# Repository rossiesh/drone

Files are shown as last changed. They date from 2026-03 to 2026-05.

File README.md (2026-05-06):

# ESP32-S3 Drone

## Status

Work in progress.

## Overview

This repository contains the firmware, 3D-print resources and documentation for a drone project based on two XIAO ESP32-S3 boards:

- one ESP32-S3 as the flight controller
- one ESP32-S3 used in the handheld

The long-term goal is a custom drone system with:

- ESP-NOW communication between handheld and flight controller
- a custom flight control stack
- an Android app connected to the handheld via USB-C for displaying telemetry data 
- 3D-printed drone parts

## Current state

The current implementation already covers some core building blocks:

- ESP-NOW communication between handheld and flight controller is set up
- the MPU6500 IMU is connected via SPI and can be read successfully
- gyroscope calibration is implemented
- 3D print resources

The project is still missing major parts required for actual flight, for example:

- control packet/telemetry packet integration
- full flight-control logic
- motor mixer logic
- Android app
- full preflight/safety/failsafe handling

## Repository structure

- [`esp32_fc/`](./esp32_fc/) ESP-IDF project for the flight controller

- [`esp32_handheld/`](./esp32_handheld/) ESP-IDF project for the handheld

- [`protocols/`](./protocols/) shared packet structures for control/telemetry communication

- [`android_app/`](./android_app/) Android application code

- [`print_resources/`](./print_resources/) 3D print files and further information

- [`documentation/`](./documentation/) project documentation such as materials and assembly information

- [`tools/`](./tools/) helper tools

## Development environment

- VS Code
- ESP-IDF extension 
- ESP-IDF v6.0
- target: esp32s3

## Documentation

- [Materials](documentation/materials.md)
- [Assembly tutorial](documentation/assembly_tutorial.md)
- [Print resources](print_resources/README.md)

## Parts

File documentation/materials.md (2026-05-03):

## Materials

- FC and controller: 2x XIAO ESP32 S3 *(~15€ for the three-pack)*
- IMU: MPU6500 *(~3€)*
- barometer: MS5611 *(~5€)*
- ESC: Sequre Blueson A2 (comes with power cables, XT60 connector and capacitor) *(~30€)*
- motors: 4x iFlight XING-E Pro 2207 2450KV (screws and self-locking nuts included) *(~35€)* or similar
- props: 4x iFlight Nazgul F5 *(~5€)*
- battery: e.g. Goldbat 4s 1500mAh LiPo *(~35€ for a two-pack)* (an additional LiPo charger is required)
- generic DC-DC 3A adjustable buck converter, e.g. MP1584EN *(~4€ for the five-pack)*
- 2.4GHz rod antenna (2.81dBi) for Seeed Studio XIAO *(~3€)*
- M3 screw set with nuts and screwdriver/ratchet wrench *(~8€ for the screw set)*, you need:
  - 24x M3x12 (16 with flats)
  - 12x M3x16 with flats
  - 6x M3x30
  - 12x locks
- M3 silicon shock absorber rings *(~3€)*, you need 18 rings
- 3D printer for the frame (Elegoo Neptune 4) *(~200€)* 
- White & black Elegoo Pla+ *(~20€ per spool)*
- soldering equipment: 
  - basic soldering iron *(~20€)*
  - 900M-T-I soldering tips recommend when working with the ESP32 & sensors *(~5€)*
  - brass wool for cleaning *(~5-10€)*
  - tip re-tiner *(~5€)*
- basic multimeter *(~15-20€)*
- high AWG cables, e.g. breadboard jumper wires
- crimping pliers with JST-XH 2.5mm connectors *(~25€ for a full set)*
- double sided tape

Most of the items I got from AliExpress.

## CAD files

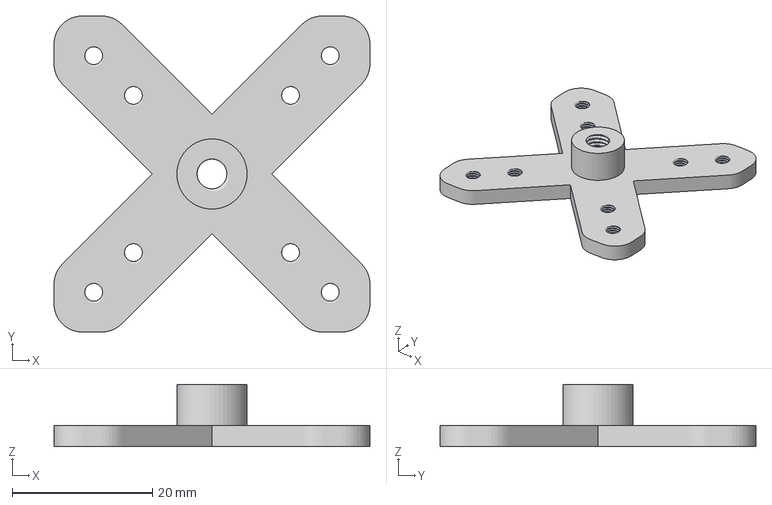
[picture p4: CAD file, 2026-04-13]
print_resources/bottom_plate.3mf
45.0 x 45.0 x 8.90 mm

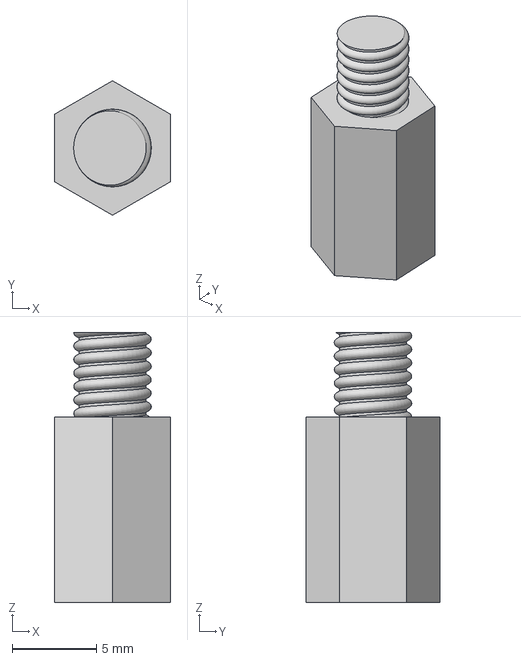
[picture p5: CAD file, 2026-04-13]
print_resources/landing_gear_long.3mf
6.90 x 7.97 x 16.0 mm

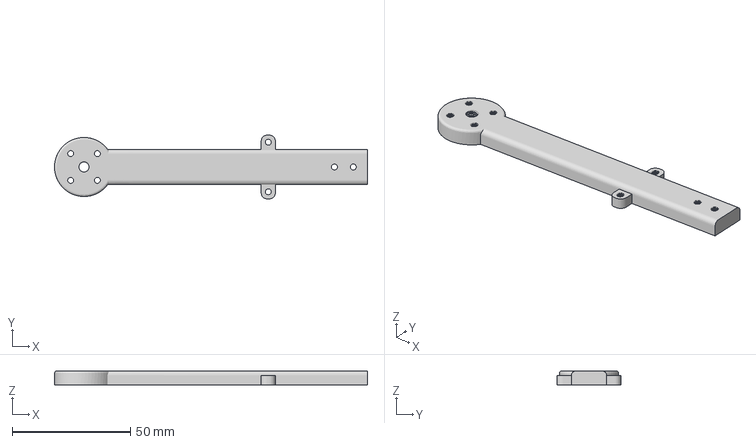
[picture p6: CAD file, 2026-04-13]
print_resources/arm.3mf
132.5 x 27.0 x 6.00 mm

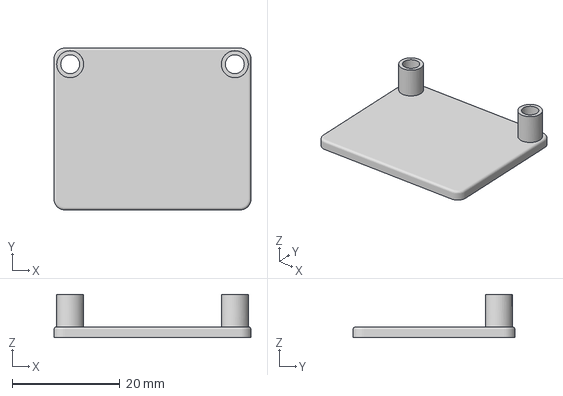
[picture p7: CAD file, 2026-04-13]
print_resources/e_plate_bottom.3mf
36.5 x 30.0 x 8.00 mm

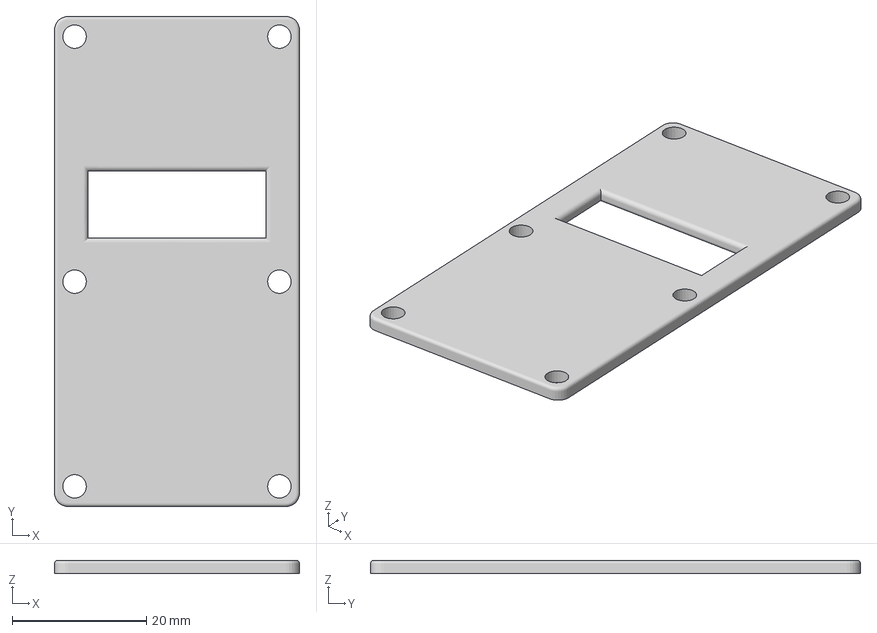
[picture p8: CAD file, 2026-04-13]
print_resources/e_plate_top.3mf
36.5 x 73.0 x 2.00 mm

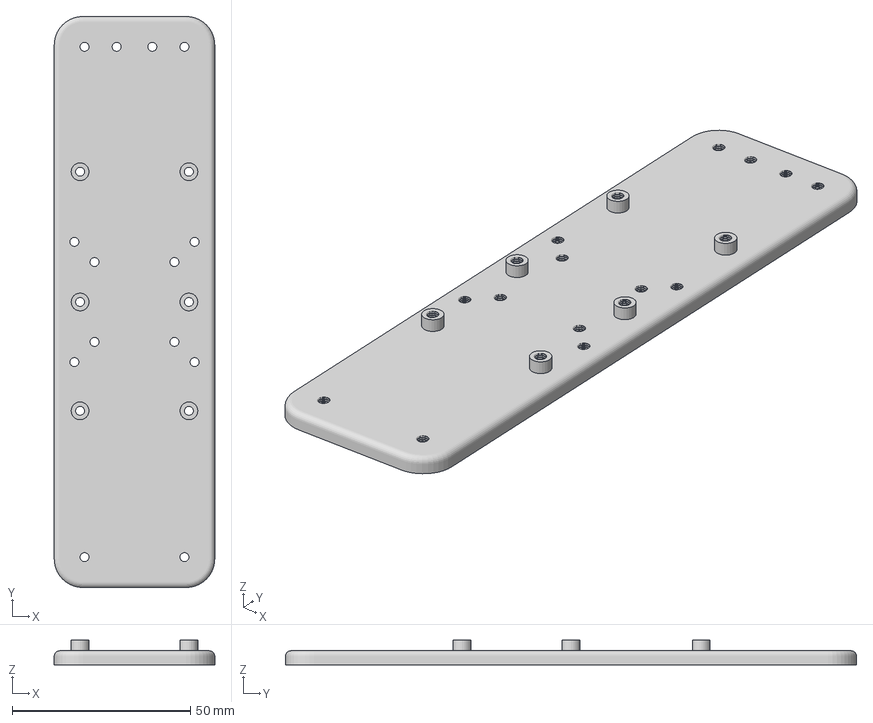
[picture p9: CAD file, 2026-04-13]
print_resources/middle_plate.3mf
45.0 x 160.0 x 7.00 mm

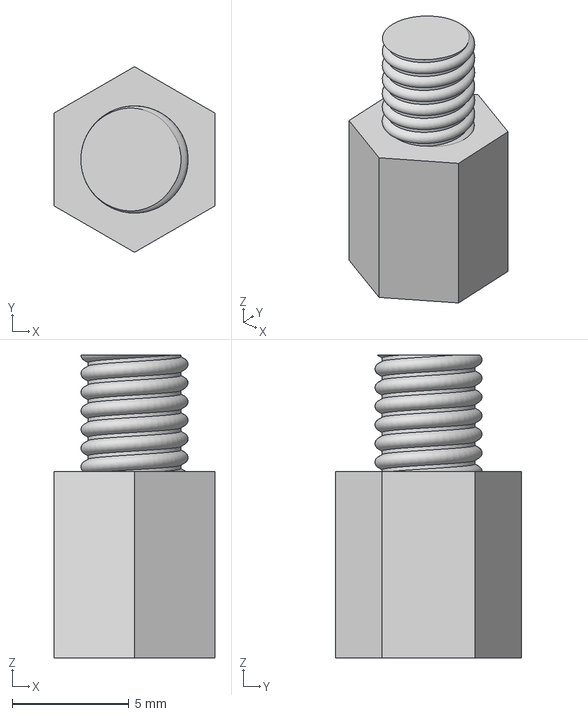
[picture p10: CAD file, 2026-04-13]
print_resources/landing_gear_short.3mf
6.90 x 7.97 x 13.0 mm

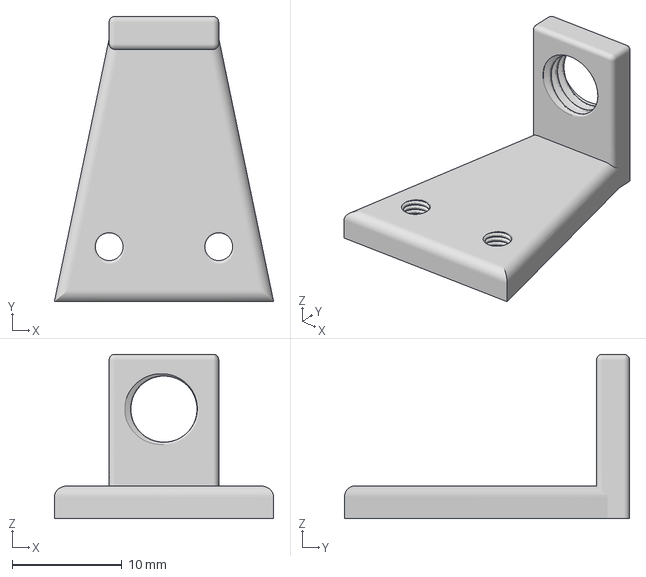
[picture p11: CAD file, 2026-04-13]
print_resources/antenna_holder.3mf
20.0 x 26.0 x 15.0 mm

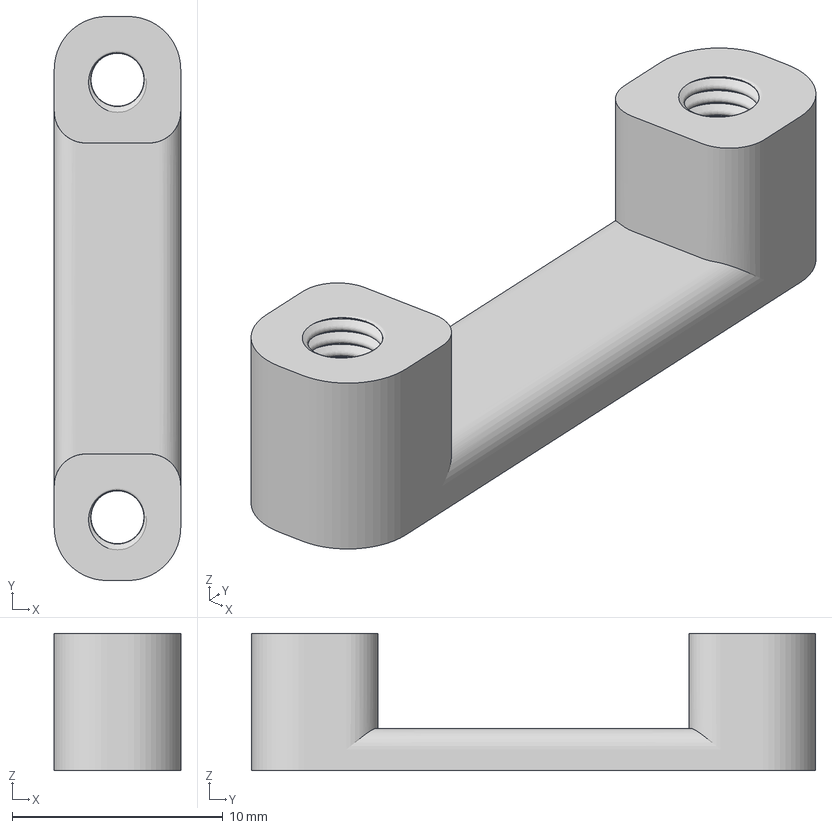
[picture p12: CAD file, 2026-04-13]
print_resources/cable_holder.3mf
6.00 x 26.8 x 6.50 mm

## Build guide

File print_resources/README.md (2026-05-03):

## General information

- printer used: Elegoo Neptune 4
- filament: Elegoo Pla+
- black Pla+ for the landing gear and plates for the electronics
- white Pla+ for the body parts and arms due to better heat reflection than black Pla+
- print arm.3mf four times
- print cable_holder.3mf four times
- print landing_gear_long.3mf four times
- print everything else one time
- use drone_arms.curaprofile only for the arms
- use drone_electronics_plates.curaprofile for:
  - e_plate_bottom.3mf
  - e_plate_top.3mf
- use drone_main_body.curaprofile for:
  - antenna_holder.3mf
  - bottom_plate.3mf
  - cable_holder.3mf
  - landing_gear_long.3mf
  - landing_gear_short.3mf
  - middle_plate.3mf

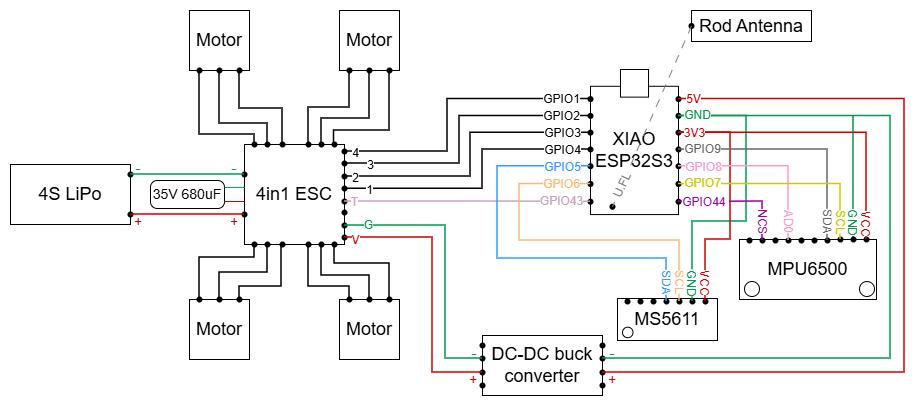
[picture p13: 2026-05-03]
documentation/assets/diagrams/wiring_diagram_drone.png

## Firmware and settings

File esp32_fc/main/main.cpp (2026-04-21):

#include <stdio.h>
#include "wifi.h"
#include "espnow.h"
#include "esp_log.h"
#include "mpu6500.h"
#include "freertos/FreeRTOS.h"
#include "freertos/task.h"

static const char *TAG = "mpu6500";

extern "C" void app_main(void)
{
    ESP_ERROR_CHECK(wifi_init());
    ESP_ERROR_CHECK(espnow_init());
    ESP_ERROR_CHECK(mpu6500_init());
    ESP_ERROR_CHECK(mpu6500_calibrate_gyro());
    ImuData imu_data = {0};
    while (true)
    {
        ESP_ERROR_CHECK(mpu6500_read_data(imu_data));
        ESP_LOGI(TAG, "a_x:%6d a_y=%6d a_z=%6d temp=%6d g_x=%6d g_y=%6d g_z=%6d", imu_data.a_x, imu_data.a_y, imu_data.a_z, imu_data.temp, imu_data.g_x, imu_data.g_y, imu_data.g_z);
        vTaskDelay(pdMS_TO_TICKS(100));
    }
}

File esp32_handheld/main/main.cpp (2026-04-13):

#include <stdio.h>
#include "control_packet.h"
#include "wifi.h"
#include "espnow.h"
#include "driver/gpio.h"
#include "freertos/FreeRTOS.h"
#include "freertos/task.h"
#include "esp_log.h"

void setup_gpio_pin(gpio_num_t gpio_num)
{
    gpio_config_t io_conf = {
        .pin_bit_mask = 1ULL << gpio_num,
        .mode = GPIO_MODE_INPUT,
        .pull_up_en = GPIO_PULLUP_ENABLE,
        .pull_down_en = GPIO_PULLDOWN_DISABLE,
        .intr_type = GPIO_INTR_DISABLE,
    };
    ESP_ERROR_CHECK(gpio_config(&io_conf));
}

extern "C" void app_main(void)
{
    static const char *TAG = "button_num";

    ESP_ERROR_CHECK(wifi_init());
    ESP_ERROR_CHECK(espnow_init());

    gpio_num_t button_1 = GPIO_NUM_4;
    gpio_num_t button_2 = GPIO_NUM_43;
    gpio_num_t button_3 = GPIO_NUM_6;
    gpio_num_t button_4 = GPIO_NUM_5;

    setup_gpio_pin(button_1);
    setup_gpio_pin(button_2);
    setup_gpio_pin(button_3);
    setup_gpio_pin(button_4);

    uint8_t test_data[] = "ping";
    // ESP_ERROR_CHECK(espnow_send_data(test_data, sizeof(test_data)));
    while (true)
    {
        if (gpio_get_level(button_1) == 0)
        {
            ESP_ERROR_CHECK(espnow_send_data(test_data, sizeof(test_data)));
            /* ControlPacket control_data={
                .packet_id=1,
                .throttle=200,
                .yaw=0,
                .pitch=0,
                .roll=0,
            };  */
            ESP_LOGI(TAG, "%d", 1);
               }
        if (gpio_get_level(button_2) == 0)
        {
            ESP_LOGI(TAG, "%d", 2);
        }
        if (gpio_get_level(button_3) == 0)
        {
            ESP_LOGI(TAG, "%d", 3);
        }
        if (gpio_get_level(button_4) == 0)
        {
            ESP_LOGI(TAG, "%d", 4);
        }
        vTaskDelay(pdMS_TO_TICKS(100));
    }
}

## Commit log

2026-03-16 tried implementing softap + websocket and connecting to it via android app. did not work due to os problems
    [main.cpp]
2026-03-17 removed esp32_mac_addresses.txt from repo
2026-04-13 initial mpu6500 spi bring-up. added protocols.
2026-04-13 deleted .gcode files and replaced with .3mf files
    [antenna_holder.3mf, arm.3mf, bottom_plate.3mf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]
2026-04-13 renamed 3mf_files folder to print_resources
    [antenna_holder.3mf, arm.3mf, bottom_plate.3mf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]
2026-04-21 reading of calibrated imu data implemented
2026-05-03 started with ms5611 sensor setup
2026-05-04 renamed esp32_controller to esp32_handheld
